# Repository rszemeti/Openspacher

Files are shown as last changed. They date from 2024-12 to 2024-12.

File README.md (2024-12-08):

This badly written nonsense is my attempt at a controller to replace the one I found lurking in a Eberspacher D5S with a canbus interface for the Renault Master. It will eventuall provide a basic control protocol to allow it to be messed with over serial, N2K and probably just a simple on/off control input so you can use these units on boats etc without needing an entire Renault Master van in tow.

There is a PCB in Eagle too, kinda.

Please bear in mind it will probably set on fire, burn down your house, cause your cat to imnplode etc.

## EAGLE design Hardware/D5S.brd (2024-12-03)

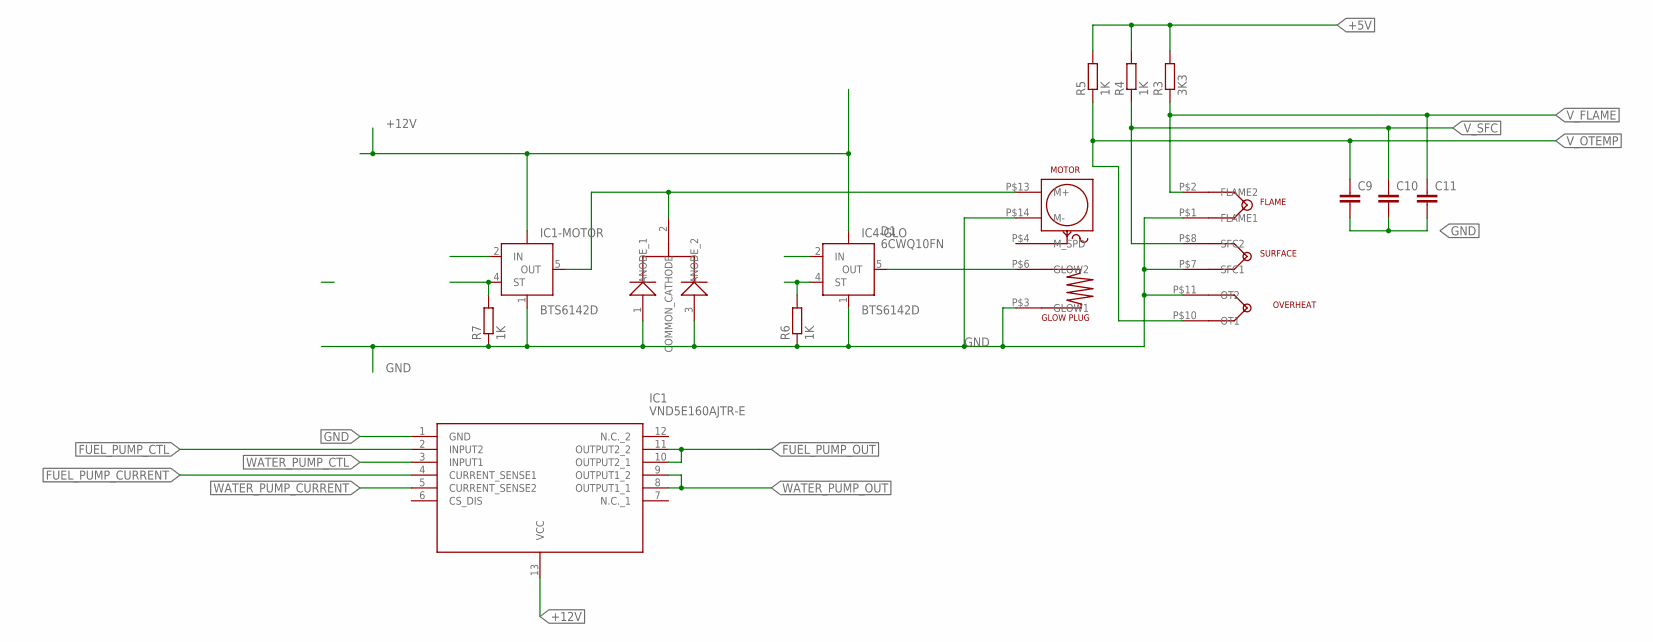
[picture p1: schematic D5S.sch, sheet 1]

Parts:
C9, C10, C11: C-EUC0603; C0603
D1: 6CWQ10FN
IC1: VND5E160AJTR-E; SOP80P600X162-13N
IC1-MOTOR, IC4-GLO: BTS6142D; TO252-5-11
R3: 3K3; R0603
R4, R5, R6, R7: 1K; R0603
U$1: D5S; PCB

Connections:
+5V: R3.2, R4.2, R5.2; also elsewhere on the board
+12V: IC1.13 (VCC), IC1-MOTOR.TAB (VBB), IC4-GLO.TAB (VBB)
FAN_CTL: IC1-MOTOR.2 (IN); also elsewhere on the board
FAN_SENSE: IC1-MOTOR.4 (ST), R7.2
FUEL_PUMP_CTL: IC1.2 (INPUT2); also elsewhere on the board
FUEL_PUMP_CURRENT: IC1.4 (CURRENT_SENSE1)
FUEL_PUMP_OUT: IC1.10 (OUTPUT2_1), IC1.11 (OUTPUT2_2)
GLOW_CTL: IC4-GLO.2 (IN); also elsewhere on the board
GLOW_SENSE: IC4-GLO.4 (ST), R6.2
GND: C9.2, C10.2, C11.2, D1.1 (ANODE_1), D1.3 (ANODE_2), IC1.1 (GND), IC1-MOTOR.1 (GND), IC4-GLO.1 (GND), R6.1, R7.1, U$1.P$1 (FLAME1), U$1.P$3 (GLOW1), U$1.P$7 (SFC1), U$1.P$11 (OT2), U$1.P$14 (M-); also elsewhere on the board
unnamed: IC4-GLO.5 (OUT), U$1.P$6 (GLOW2)
unnamed: D1.2 (COMMON_CATHODE), IC1-MOTOR.5 (OUT), U$1.P$13 (M+)
V_FLAME: C11.1, R3.1, U$1.P$2 (FLAME2); also elsewhere on the board
V_OTEMP: C9.1, R5.1, U$1.P$10 (OT1); also elsewhere on the board
V_SFC: C10.1, R4.1, U$1.P$8 (SFC2); also elsewhere on the board
WATER_PUMP_CTL: IC1.3 (INPUT1); also elsewhere on the board
WATER_PUMP_CURRENT: IC1.5 (CURRENT_SENSE2)
WATER_PUMP_OUT: IC1.8 (OUTPUT1_1), IC1.9 (OUTPUT1_2)

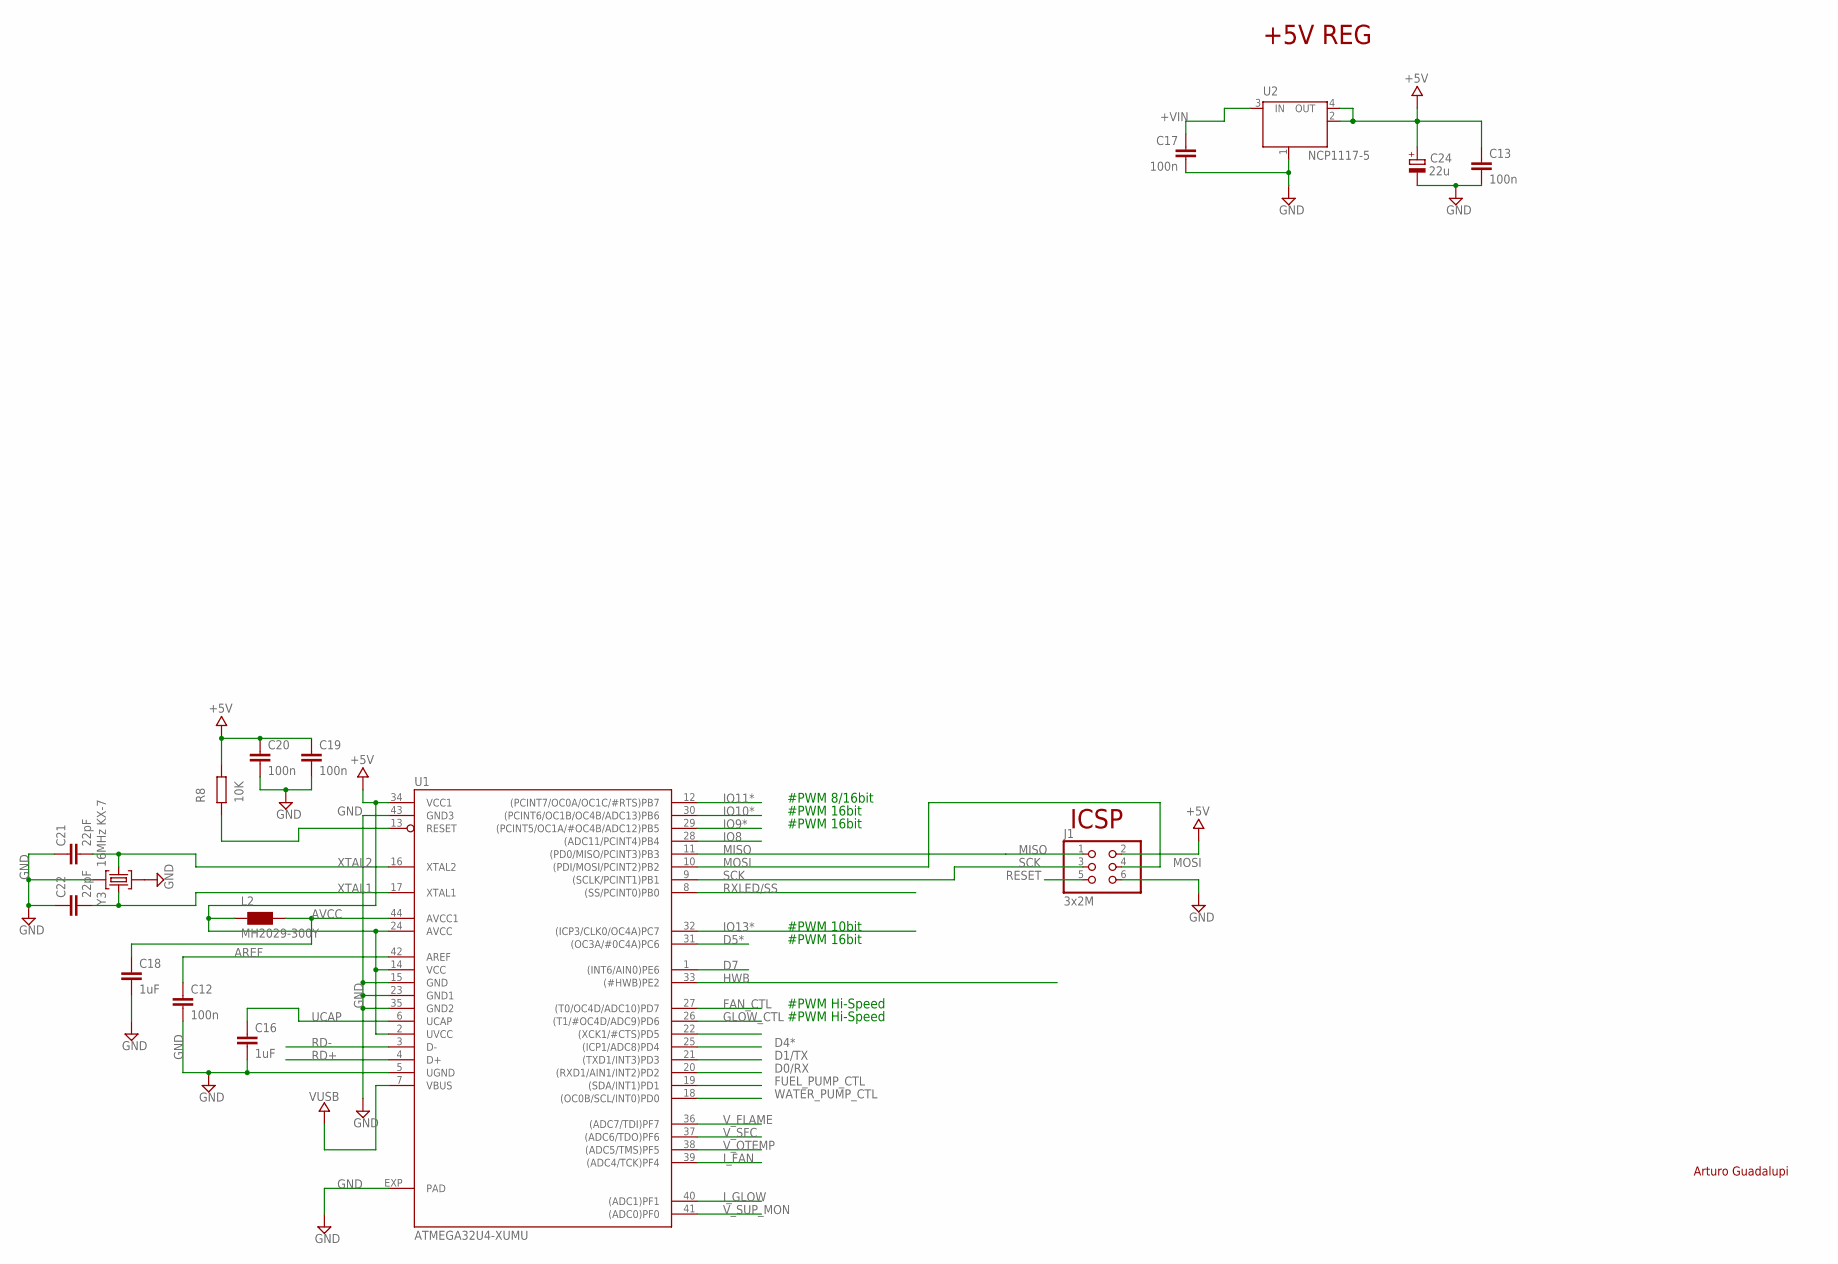
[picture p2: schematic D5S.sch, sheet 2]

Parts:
C12, C13, C17, C19, C20: 100n; C0402
C16, C18: 1uF; C0402
C21, C22: 22pF; C0402
C24: 22u; SMC_B
J1: 3x2M; 2X03
L2: MH2029-300Y; 0805
R8: 10K; R0402
U1: ATMEGA32U4-XUMU; QFN44ML7X7
U2: NCP1117-5; SOT223
Y3: 16MHz KX-7; CRYSTAL-3.2-2.5

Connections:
+5V: C13.1, C19.1, C20.1, C24.+, J1.2, L2.1, R8.1, U1.2 (UVCC), U1.14 (VCC), U1.24 (AVCC), U1.34 (VCC1), U2.2 (OUT), U2.4 (OUT); also elsewhere on the board
+VIN: C17.1, U2.3 (IN)
AREF: C12.1, U1.42 (AREF)
AVCC: C18.1, L2.2, U1.44 (AVCC1)
D0/RX: U1.20 ((RXD1/AIN1/INT2)PD2)
D1/TX: U1.21 ((TXD1/INT3)PD3)
D4*: U1.25 ((ICP1/ADC8)PD4)
D5*: U1.31 ((OC3A/#0C4A)PC6)
D7: U1.1 ((INT6/AIN0)PE6)
FAN_CTL: U1.27 ((T0/OC4D/ADC10)PD7); also elsewhere on the board
FUEL_PUMP_CTL: U1.19 ((SDA/INT1)PD1); also elsewhere on the board
GLOW_CTL: U1.26 ((T1/#OC4D/ADC9)PD6); also elsewhere on the board
GND: C12.2, C13.2, C16.2, C17.2, C18.2, C19.2, C20.2, C21.1, C22.1, C24.-, J1.6, U1.5 (UGND), U1.15 (GND), U1.23 (GND1), U1.35 (GND2), U1.43 (GND3), U1.EXP (PAD), U2.1 (GND/ADJ), Y3.2 (GND), Y3.4 (GND); also elsewhere on the board
HWB: U1.33 ((#HWB)PE2)
IO8: U1.28 ((ADC11/PCINT4)PB4)
IO9*: U1.29 ((PCINT5/OC1A/#OC4B/ADC12)PB5)
IO10*: U1.30 ((PCINT6/OC1B/OC4B/ADC13)PB6)
IO11*: U1.12 ((PCINT7/OC0A/OC1C/#RTS)PB7)
IO13*: U1.32 ((ICP3/CLK0/OC4A)PC7)
I_FAN: U1.39 ((ADC4/TCK)PF4)
I_GLOW: U1.40 ((ADC1)PF1)
MISO: J1.1, U1.11 ((PD0/MISO/PCINT3)PB3)
MOSI: J1.4, U1.10 ((PDI/MOSI/PCINT2)PB2)
RD+: U1.4 (D+)
RD-: U1.3 (D-)
RESET: J1.5, R8.2, U1.13 (RESET)
RXLED/SS: U1.8 ((SS/PCINT0)PB0)
SCK: J1.3, U1.9 ((SCLK/PCINT1)PB1)
TXLED: U1.22 ((XCK1/#CTS)PD5)
UCAP: C16.1, U1.6 (UCAP)
VUSB: U1.7 (VBUS)
V_FLAME: U1.36 ((ADC7/TDI)PF7); also elsewhere on the board
V_OTEMP: U1.38 ((ADC5/TMS)PF5); also elsewhere on the board
V_SFC: U1.37 ((ADC6/TDO)PF6); also elsewhere on the board
V_SUP_MON: U1.41 ((ADC0)PF0)
WATER_PUMP_CTL: U1.18 ((OC0B/SCL/INT0)PD0); also elsewhere on the board
XTAL1: C22.2, U1.17 (XTAL1), Y3.3 (C2)
XTAL2: C21.2, U1.16 (XTAL2), Y3.1 (C1)

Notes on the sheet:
+5V REG
ICSP
#PWM Hi-Speed
#PWM 16bit
#PWM 10bit
#PWM 8/16bit
Arturo Guadalupi

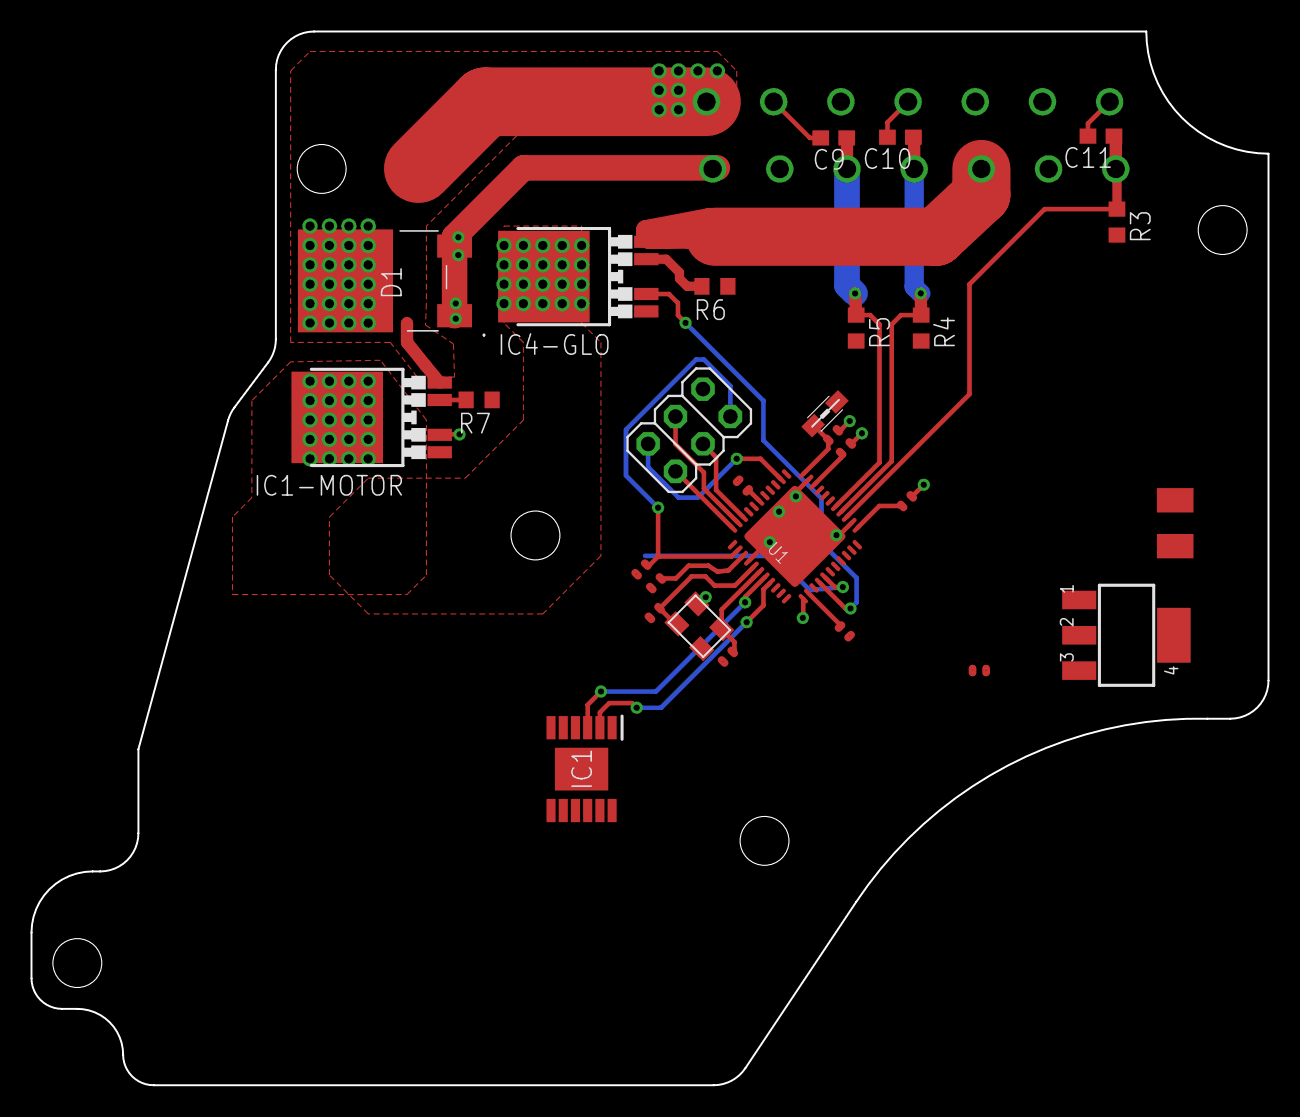
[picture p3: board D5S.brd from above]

Board: 4 copper layers, 81.0 x 69.0 mm, 29 parts (0 on the bottom side), 26 nets.

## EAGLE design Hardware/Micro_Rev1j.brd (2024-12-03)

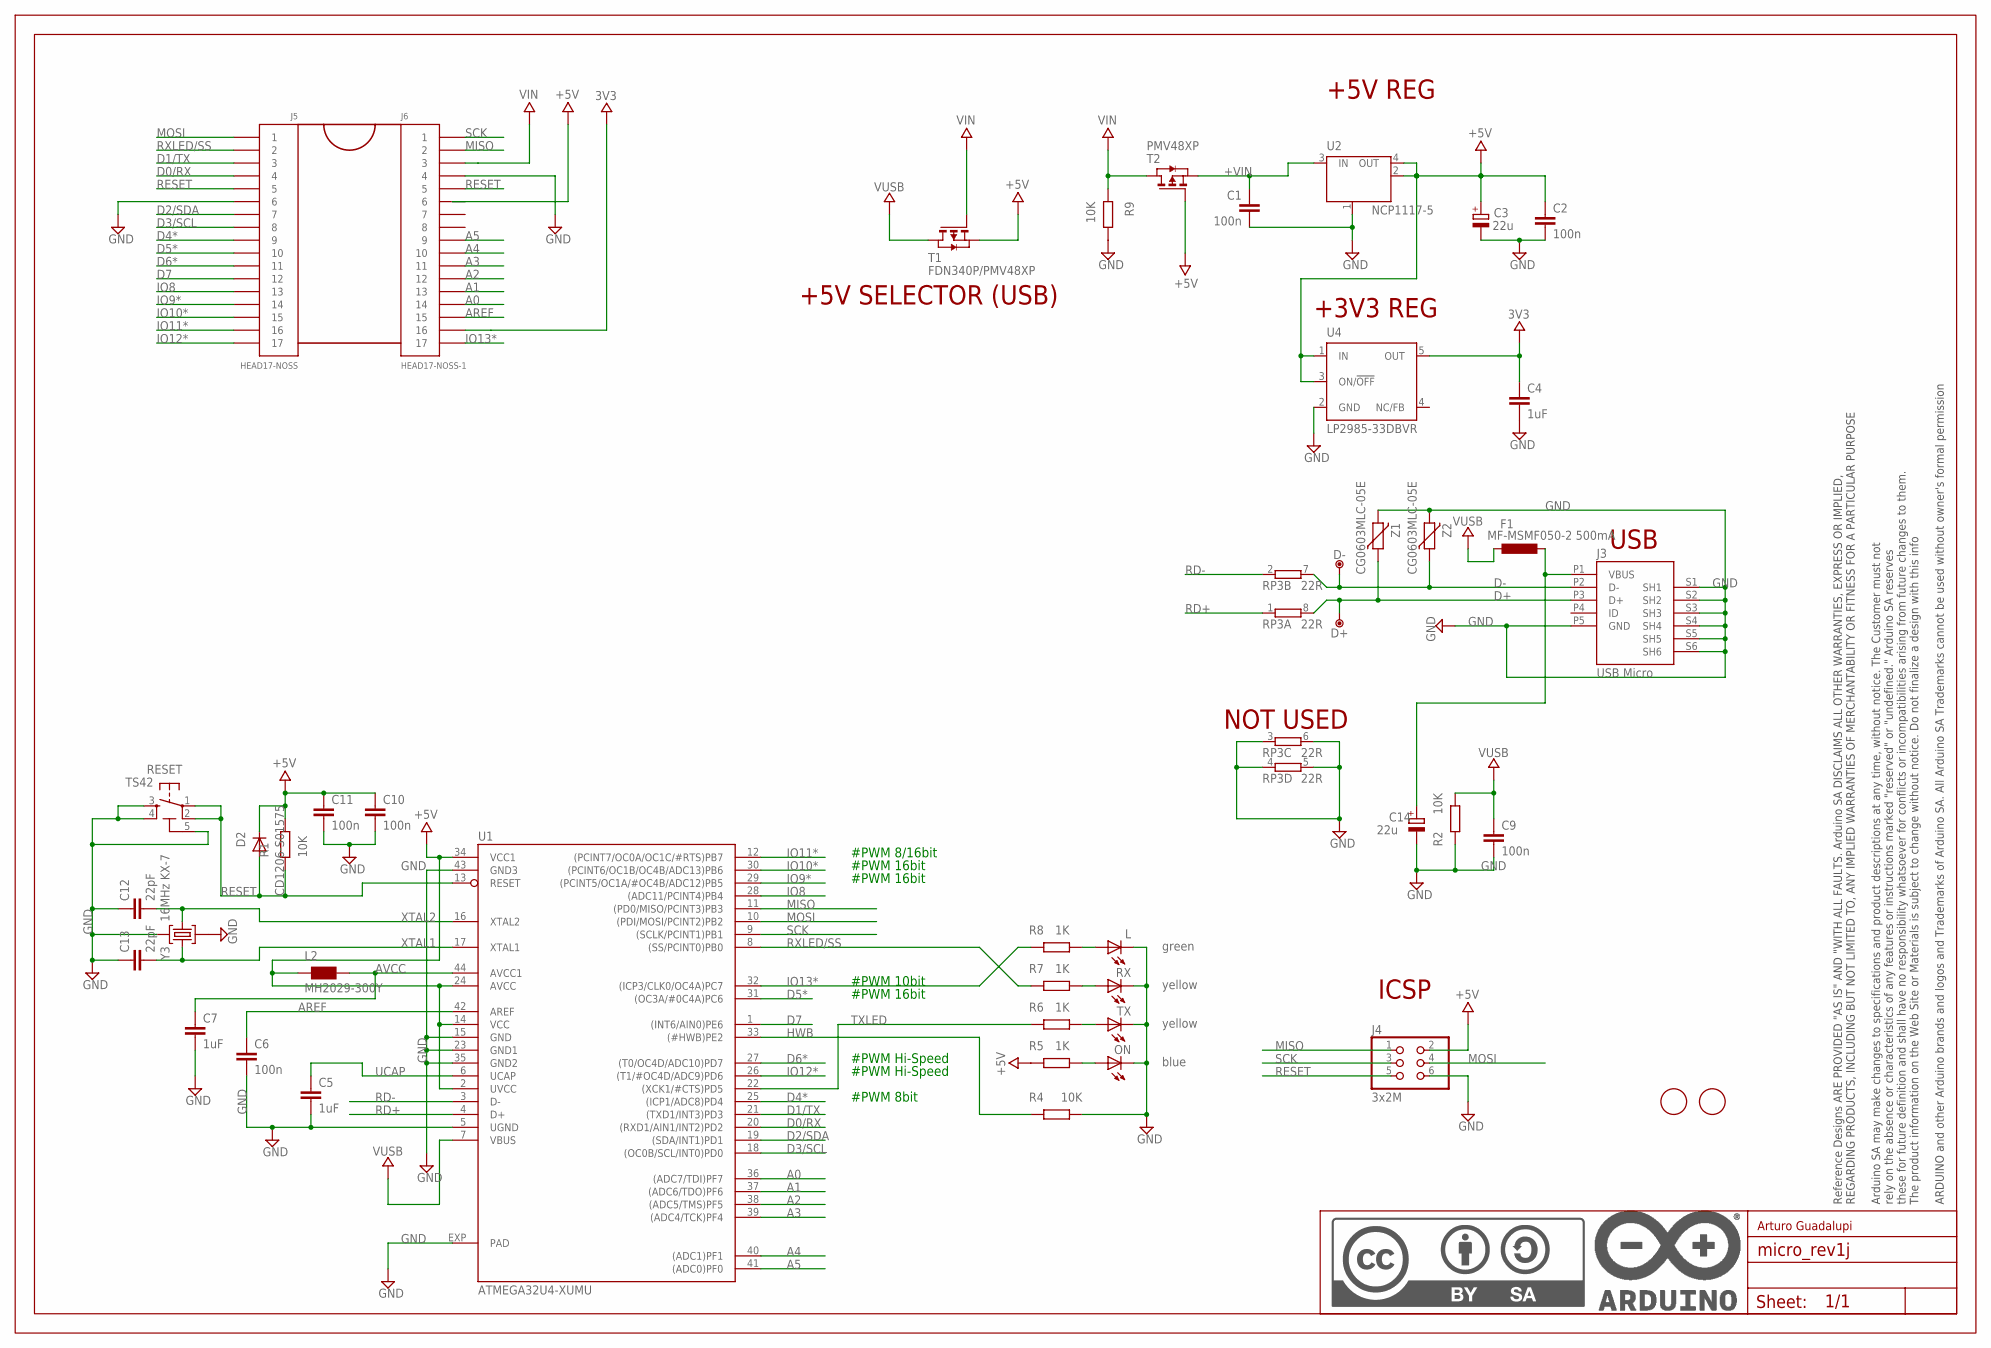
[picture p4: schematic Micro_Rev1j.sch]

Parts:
C1, C2, C6, C9, C10, C11: 100n; C0402
C3, C14: 22u; SMC_B
C4, C5, C7: 1uF; C0402
C12, C13: 22pF; C0402
D2: CD1206-S01575; MINIMELF
D+: DNP; TP-1.00MM
D-: DNP; TP-1.00MM
F1: MF-MSMF050-2 500mA; L1812
FRAME1: DNP; FRAME
J3: USB Micro; CON2_USB_MICRO_B_AT
J4: 3x2M; 2X03
J5: HEAD17-NOSS
J6: HEAD17-NOSS-1
L: green; CHIPLED_0805
L2: MH2029-300Y; 0805
ON: blue; CHIPLED_0805
R1, R2, R4, R9: 10K; R0402
R5, R6, R7, R8: 1K; R0402
RESET: TS42
RP3: 22R; CAY16
RX: yellow; CHIPLED_0805
T1: FDN340P/PMV48XP; SOT-23
T2: PMV48XP; SOT-23
TX: yellow; CHIPLED_0805
U1: ATMEGA32U4-XUMU; QFN44ML7X7
U2: NCP1117-5; SOT223
U4: LP2985-33DBVR; SOT23-DBV
U$37, U$53: DNP; FD-1-1.5
Y3: 16MHz KX-7; CRYSTAL-3.2-2.5
Z1, Z2: CG0603MLC-05E; CT/CN0603

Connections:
3V3: C4.1, J6.16, U4.5 (OUT)
+5V: C2.1, C3.+, C10.1, C11.1, D2.C, J4.2, J6.6, L2.1, R1.1, R5.1, T1.2 (S), T2.3 (G), U1.2 (UVCC), U1.14 (VCC), U1.24 (AVCC), U1.34 (VCC1), U2.2 (OUT), U2.4 (OUT), U4.1 (IN), U4.3 (ON/!OFF)
+VIN: C1.1, T2.2 (S), U2.3 (IN)
A0: J6.14, U1.36 ((ADC7/TDI)PF7)
A1: J6.13, U1.37 ((ADC6/TDO)PF6)
A2: J6.12, U1.38 ((ADC5/TMS)PF5)
A3: J6.11, U1.39 ((ADC4/TCK)PF4)
A4: J6.10, U1.40 ((ADC1)PF1)
A5: J6.9, U1.41 ((ADC0)PF0)
AREF: C6.1, J6.15, U1.42 (AREF)
AVCC: C7.1, L2.2, U1.44 (AVCC1)
D0/RX: J5.4, U1.20 ((RXD1/AIN1/INT2)PD2)
D1/TX: J5.3, U1.21 ((TXD1/INT3)PD3)
D2/SDA: J5.7, U1.19 ((SDA/INT1)PD1)
D3/SCL: J5.8, U1.18 ((OC0B/SCL/INT0)PD0)
D4*: J5.9, U1.25 ((ICP1/ADC8)PD4)
D5*: J5.10, U1.31 ((OC3A/#0C4A)PC6)
D6*: J5.11, U1.27 ((T0/OC4D/ADC10)PD7)
D7: J5.12, U1.1 ((INT6/AIN0)PE6)
D+: D+.X, J3.P3 (D+), RP3.8 (2), Z1.1
D-: D-.X, J3.P2 (D-), RP3.7 (2), Z2.1
GND: C1.2, C2.2, C3.-, C4.2, C5.2, C6.2, C7.2, C9.2, C10.2, C11.2, C12.1, C13.1, C14.-, J3.P5 (GND), J3.S1 (SH1), J3.S2 (SH2), J3.S3 (SH3), J3.S4 (SH4), J3.S5 (SH5), J3.S6 (SH6), J4.6, J5.6, J6.4, L.C, ON.C, R2.1, R4.2, R9.1, RESET.3, RESET.4, RESET.5 (5-GND), RP3.3 (1), RP3.4 (1), RP3.5 (2), RP3.6 (2), RX.C, TX.C, U1.5 (UGND), U1.15 (GND), U1.23 (GND1), U1.35 (GND2), U1.43 (GND3), U1.EXP (PAD), U2.1 (GND/ADJ), U4.2 (GND), Y3.2 (GND), Y3.4 (GND), Z1.2, Z2.2
HWB: R4.1, U1.33 ((#HWB)PE2)
IO8: J5.13, U1.28 ((ADC11/PCINT4)PB4)
IO9*: J5.14, U1.29 ((PCINT5/OC1A/#OC4B/ADC12)PB5)
IO10*: J5.15, U1.30 ((PCINT6/OC1B/OC4B/ADC13)PB6)
IO11*: J5.16, U1.12 ((PCINT7/OC0A/OC1C/#RTS)PB7)
IO12*: J5.17, U1.26 ((T1/#OC4D/ADC9)PD6)
IO13*: J6.17, R8.1, U1.32 ((ICP3/CLK0/OC4A)PC7)
MISO: J4.1, J6.2, U1.11 ((PD0/MISO/PCINT3)PB3)
MOSI: J4.4, J5.1, U1.10 ((PDI/MOSI/PCINT2)PB2)
unnamed: R7.2, RX.A
unnamed: ON.A, R5.2
unnamed: R6.2, TX.A
unnamed: L.A, R8.2
RD+: RP3.1, U1.4 (D+)
RD-: RP3.2 (1), U1.3 (D-)
RESET: D2.A, J4.5, J5.5, J6.5, R1.2, RESET.1, RESET.2, U1.13 (RESET)
RXLED/SS: J5.2, R7.1, U1.8 ((SS/PCINT0)PB0)
SCK: J4.3, J6.1, U1.9 ((SCLK/PCINT1)PB1)
TXLED: R6.1, U1.22 ((XCK1/#CTS)PD5)
UCAP: C5.1, U1.6 (UCAP)
VIN: J6.3, R9.2, T1.3 (G), T2.1 (D)
VUSB: C9.1, F1.2, R2.2, T1.1 (D), U1.7 (VBUS)
VUSBD: C14.+, F1.1, J3.P1 (VBUS)
XTAL1: C13.2, U1.17 (XTAL1), Y3.3 (C2)
XTAL2: C12.2, U1.16 (XTAL2), Y3.1 (C1)

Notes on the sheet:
+5V REG
ICSP
USB
+5V SELECTOR (USB)
NOT USED
+3V3 REG
#PWM 8bit
#PWM Hi-Speed
#PWM 16bit
#PWM 10bit
#PWM 8/16bit
Arturo Guadalupi

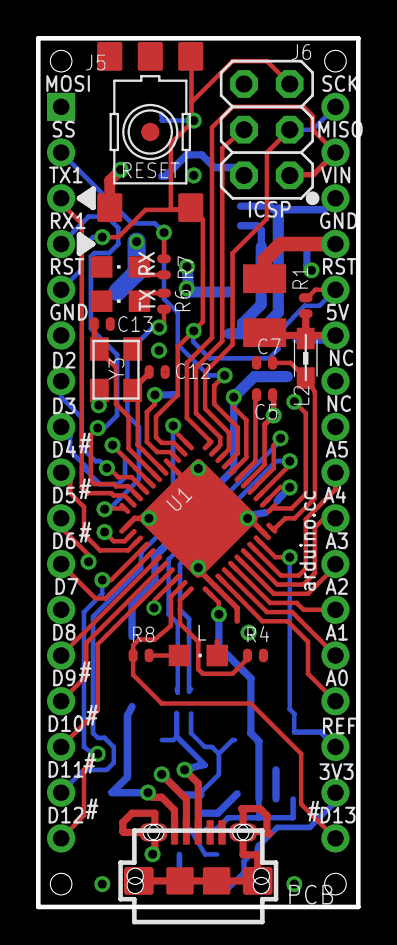
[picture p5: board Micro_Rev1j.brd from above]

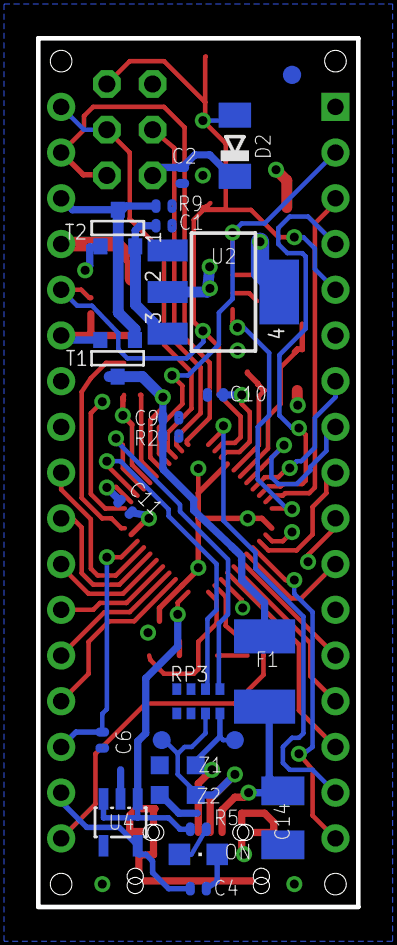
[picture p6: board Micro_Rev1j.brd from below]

Board: 4 copper layers, 17.8 x 48.3 mm, 47 parts (22 on the bottom side), 47 nets.

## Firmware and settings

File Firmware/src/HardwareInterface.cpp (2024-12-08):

#include "HardwareInterface.h"
#include "HardwareConfig.h"

// Initialize all hardware components
void HardwareInterface::init() {
    // Set digital output pins
    pinMode(fanPin, OUTPUT);
    pinMode(fuelPumpPin, OUTPUT);
    pinMode(waterPumpPin, OUTPUT);
    pinMode(blowerPin, OUTPUT);
    pinMode(glowVoltsPin, OUTPUT);
    pinMode(waterPumpSpeedPin, OUTPUT);
    pinMode(powerCtlPin, OUTPUT);

    // Default states: LOW or OFF
    digitalWrite(fanPin, LOW);
    digitalWrite(fuelPumpPin, LOW);
    digitalWrite(waterPumpPin, LOW);
    digitalWrite(blowerPin, LOW);
    digitalWrite(glowVoltsPin, LOW);
    digitalWrite(waterPumpSpeedPin, LOW);
    digitalWrite(powerCtlPin, LOW);
}

// Output controls
void HardwareInterface::setFanSpeed(uint8_t speed) {
    analogWrite(fanPin, speed);
}

void HardwareInterface::setFuelPumpSpeed(uint8_t speed) {
    analogWrite(fuelPumpPin, speed);
}

void HardwareInterface::setWaterPumpState(bool state) {
    digitalWrite(waterPumpPin, state ? HIGH : LOW);
}

void HardwareInterface::setBlowerState(bool state) {
    digitalWrite(blowerPin, state ? HIGH : LOW);
}

void HardwareInterface::setGlowState(bool state) {
    analogWrite(blowerPin, state ? GLOW_VOLTS_ON : GLOW_VOLTS_OFF);
}

void HardwareInterface::setWaterPumpSpeed(uint8_t speed) {
    analogWrite(waterPumpSpeedPin, speed);
}

void HardwareInterface::setPowerControl(bool state) {
    digitalWrite(powerCtlPin, state ? HIGH : LOW);
}

// Input reading
int HardwareInterface::readFlameSensor() {
    return analogRead(flameSensePin);
}

int HardwareInterface::readSurfaceSensor() {
    return analogRead(surfaceSensePin);
}

int HardwareInterface::readOvertempSensor() {
    return analogRead(overtempSensePin);
}

// Current sensing
int HardwareInterface::readFanCurrent() {
    return analogRead(fanCurrentSensePin);
}

int HardwareInterface::readGlowCurrent() {
    return analogRead(glowCurrentSensePin);
}

int HardwareInterface::readWaterPumpCurrent() {
    return analogRead(waterPumpCurrentSensePin);
}

// Interpolation function with extrapolation
int HardwareInterface::interpolate(int rawValue, const VoltageTempMapping mapping[], size_t size) {
    for (size_t i = 0; i < size - 1; i++) {
        int x1 = mapping[i].voltage;
        int y1 = mapping[i].temperature;
        int x2 = mapping[i + 1].voltage;
        int y2 = mapping[i + 1].temperature;

        // Check if rawValue is within the current range
        if (rawValue >= x1 && rawValue <= x2) {
            // Linear interpolation formula
            return y1 + (y2 - y1) * (rawValue - x1) / (x2 - x1);
        }
    }

    // Extrapolate before the first point
    if (rawValue < mapping[0].voltage) {
        int x1 = mapping[0].voltage;
        int y1 = mapping[0].temperature;
        int x2 = mapping[1].voltage;
        int y2 = mapping[1].temperature;
        return y1 + (y2 - y1) * (rawValue - x1) / (x2 - x1);
    }

    // Extrapolate after the last point
    if (rawValue > mapping[size - 1].voltage) {
        int x1 = mapping[size - 2].voltage;
        int y1 = mapping[size - 2].temperature;
        int x2 = mapping[size - 1].voltage;
        int y2 = mapping[size - 1].temperature;
        return y1 + (y2 - y1) * (rawValue - x1) / (x2 - x1);
    }

    return 0; // Default fallback
}

// Get water temperature
int HardwareInterface::getWaterTemp() {
    int rawValue = this->readSurfaceSensor();
    return interpolate(rawValue, waterTempMapping, sizeof(waterTempMapping) / sizeof(waterTempMapping[0]));
}

// Get flame temperature
int HardwareInterface::getFlameTemp() {
    int rawValue = this->readFlameSensor();
    return interpolate(rawValue, flameTempMapping, sizeof(flameTempMapping) / sizeof(flameTempMapping[0]));
}

// Get over-temperature value
int HardwareInterface::getOverTemp() {
    int rawValue = this->readOvertempSensor();
    return interpolate(rawValue, overTempMapping, sizeof(overTempMapping) / sizeof(overTempMapping[0]));
}

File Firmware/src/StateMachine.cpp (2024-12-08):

#include "StateMachine.h"
#include "HardwareInterface.h"
#include "Stages.h"

// Global pointer for condition lambdas
static StateMachine* smInstance = nullptr;

State StateMachine::largeCondition() {
    if (smInstance) {
        int waterTemp = smInstance->hardware.getWaterTemp();

        if (waterTemp > OVERTEMP_THRESHOLD) {
            return State::SHUTDOWN;
        } else if (waterTemp > LARGE_TO_SMALL_THRESHOLD) {
            return State::SMALL;
        }
    }
    return State::LARGE;
}


State StateMachine::smallCondition() {
    if (smInstance) {
        int waterTemp = smInstance->hardware.getWaterTemp();

        if (waterTemp > OVERTEMP_THRESHOLD) {
            return State::SHUTDOWN;
        } else if (waterTemp < SMALL_TO_LARGE_THRESHOLD) {
            return State::LARGE;
        }
    }
    return State::SMALL;
}

// Linear interpolation helper
int linearInterpolate(int start, int end, unsigned long elapsedTime, unsigned long duration) {
    float progress = static_cast<float>(elapsedTime) / (duration * 1000);
    if (progress > 1.0) progress = 1.0; // Clamp progress
    return start + static_cast<int>((end - start) * progress);
}

// Constructor
StateMachine::StateMachine(HardwareInterface& hw) : hardware(hw), currentState(IDLE), stageStartTime(0), currentStageIndex(0),
                                                    currentStages(nullptr), totalStages(0), nextState(IDLE),
                                                    runSignal(false) {
    smInstance = this;
}

// Initialize the state machine
void StateMachine::init() {
    Serial.begin(9600);
    resetHandler(IDLE);
}

// Set the RUN signal
void StateMachine::setRunSignal(bool run) {
    if (runSignal != run) {
        runSignal = run;
        if (!runSignal && currentState != SHUTDOWN) {
            currentState = SHUTDOWN;
            resetHandler(SHUTDOWN);
        }
    }
}

// Tick the state machine
void StateMachine::tick() {
    if (currentState == IDLE && runSignal) {
        currentState = START;
        resetHandler(START);
    }

    tickHandler();
}

// Reset the stage handler for a given state
void StateMachine::resetHandler(State state) {
    switch (state) {
        case SHUTDOWN:
            currentStages = shutdownStages;
            totalStages = shutdownStagesCount;
            nextState = IDLE;
            break;
        case START:
            currentStages = startStages;
            totalStages = startStagesCount;
            nextState = LARGE; // Transition to LARGE after START
            break;
        case LARGE: // Renamed from HIGH
            currentStages = largeStages;
            totalStages = largeStagesCount;
            nextState = SMALL; // Transition to SMALL
            break;
        case SMALL: // Renamed from LOW
            currentStages = smallStages;
            totalStages = smallStagesCount;
            nextState = LARGE; // Transition to LARGE
            break;
        default:
            currentStages = nullptr;
            totalStages = 0;
            break;
    }
    currentStageIndex = 0;
    stageStartTime = millis();
}

void StateMachine::tickHandler() {
    if (currentStageIndex >= totalStages) {
        // Transition to the next state
        currentState = nextState;
        resetHandler(currentState);
        return;
    }

    Stage& currentStage = currentStages[currentStageIndex];

    // Log the stage message
    Serial.println(currentStage.message);

    // Set digital states via hardware abstraction
    hardware.setWaterPumpState(currentStage.waterPumpState);
    hardware.setBlowerState(currentStage.blowerState);
    hardware.setGlowState(currentStage.glowState);

    // Calculate elapsed time
    unsigned long elapsedTime = millis() - stageStartTime;

    // Interpolate analog values
    int interpolatedFanSpeed = linearInterpolate(currentStage.fanSpeed.start, currentStage.fanSpeed.end, elapsedTime, currentStage.duration);
    int interpolatedFuelPump = linearInterpolate(currentStage.fuelPump.start, currentStage.fuelPump.end, elapsedTime, currentStage.duration);

    // Write interpolated values to hardware
    hardware.setFanSpeed(interpolatedFanSpeed);
    hardware.setFuelPumpSpeed(interpolatedFuelPump);

    // Log interpolated values
    Serial.print("Fan Speed: ");
    Serial.println(interpolatedFanSpeed);
    Serial.print("Fuel Pump: ");
    Serial.println(interpolatedFuelPump);

    // Check if the stage is complete
    if (elapsedTime >= currentStage.duration * 1000) {
        currentStageIndex++;
        stageStartTime = millis();

        // Final stage logic
        if (currentStageIndex >= totalStages) {
            State transitionState = currentStage.condition ? currentStage.condition() : nextState;

            // Handle state transition
            if (transitionState != currentState) {
                Serial.println("Transitioning to next state.");
                currentState = transitionState;
                resetHandler(currentState);
            }
        }
    }
}

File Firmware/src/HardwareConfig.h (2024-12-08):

#ifndef HARDWARE_CONFIG_H
#define HARDWARE_CONFIG_H
#include <Arduino.h>

// Pin Definitions
const int fanPin = 5;
const int fuelPumpPin = 6;
const int waterPumpPin = 7;
const int blowerPin = 8;
const int glowVoltsPin = 9;
const int waterPumpSpeedPin = 10;
const int powerCtlPin = 11;

// Additional Analog Pins
const int surfaceSensePin = A0;
const int overtempSensePin = A1;
const int flameSensePin = A2;
const int fanCurrentSensePin = A3;
const int glowCurrentSensePin = A4;
const int waterPumpCurrentSensePin = A5;

// Custom Mapping Struct
struct VoltageTempMapping {
    int voltage;   // Input voltage
    int temperature; // Corresponding temperature
};

// Voltage-Temperature Mappings (Fixed-Size Arrays)
const VoltageTempMapping waterTempMapping[] = {
    {0, 20},   // 0V corresponds to 20°C
    {128, 50}, // Midpoint 128 corresponds to 50°C
    {250, 100} // Max voltage corresponds to 100°C
};

const VoltageTempMapping flameTempMapping[] = {
    {0, 100},  // 0V corresponds to 100°C
    {128, 300}, // Midpoint 128 corresponds to 300°C
    {250, 600}  // Max voltage corresponds to 600°C
};

const VoltageTempMapping overTempMapping[] = {
    {0, 50},   // 0V corresponds to 50°C
    {128, 75}, // Midpoint 128 corresponds to 75°C
    {250, 150} // Max voltage corresponds to 150°C
};

#endif // HARDWARE_CONFIG_H

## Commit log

2024-12-03 Stuff from laptop
    [D5S.brd, D5S.sch, Micro_Rev1j.brd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]
2024-12-06 Arduino initial transplation from Python statemachine
2024-12-08 Interpolation and better structure to define the stages
    All the various tage timing etc is in the header . file, just dummy data for now.
2024-12-08 Further tweakage
    Runtimes and sequences now correct from D5 manual
    [HardwareInterface.cpp, Stages.h, StateMachine.cpp]
2024-12-08 help functions update
    end stage handlers updated

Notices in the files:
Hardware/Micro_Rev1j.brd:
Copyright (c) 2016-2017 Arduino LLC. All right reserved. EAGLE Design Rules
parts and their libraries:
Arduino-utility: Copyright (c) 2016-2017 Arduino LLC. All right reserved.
